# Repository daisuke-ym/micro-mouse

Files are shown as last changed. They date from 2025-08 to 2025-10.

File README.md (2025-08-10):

# マイクロマウスを作る

## はじめに

マイクロマウスは自立型ロボットが自律的に（自分の力だけで）迷路を探索し、 ゴールまで到達するものです。

競技会もあります。
詳細は
[公益財団法人ニューテクノロジー振興財団](https://www.ntf.or.jp/mouse/) 
を参照してください。

## ここで作るマイクロマウス

上記競技会ではクラシッククラスとハーフサイズクラスがありますが、
ここでは1区画180㎜のクラシッククラスを作ります。

[RT ROBOT SHOP](https://www.rt-shop.jp/index.php?main_page=product_info&products_id=4229)
等でキットが販売されていますが、高価なため個人や学生が手を出すには敷居が高いです。

そこで、3Dプリンタ、我らの秋月電子通商、中国のプリント基板業者を駆使することで
1万円以内で製作できることを目指しました。

ただし、採用しているステッピングモーター（28BYJ-48）は回転速度が遅い[^1]ため、
上記競技会で完走するのは難しいです。
主に教材用と考えてもらえればと思います。

## 主要部品

| 構成部品 | 仕様等 |
|-|-|
| マイコン | [ESP32 DevKitC](https://akizukidenshi.com/catalog/g/g115673/) |
| モーター | [28BYJ-48](https://akizukidenshi.com/catalog/g/g113256/) |
| シャーシ | 専用設計プリント基板と兼用 |
| タイヤ | 3Dプリント、TAMIYA 70144ボールキャスター |
| 電源 | 1.2V Ni-MH電池 または アルカリ乾電池 x4本 |
| 赤外線LED | [OSI5FU5111C-40](https://akizukidenshi.com/catalog/g/g103261/) |
| フォトトランジスタ | [L-51ROPT1D1](https://akizukidenshi.com/catalog/g/g104211/) |

## 開発環境

- Arduino IDE
- ESP32 ツールチェイン
- [Unistep2_mod](https://github.com/daisuke-ym/Unistep2_mod)
ライブラリ（動的に回転速度を変更できるようにしたもの）

[^1]: Unistep2 ライブラリを用いてほぼ最高速度で回しても約15rpmなので、
1区画進むのに約4秒かかります。
大会では16x16区画、256区画あるので、全探索するのに15分以上かかるため、
偶然を除いて競技時間10分以内に完走することは不可能です。

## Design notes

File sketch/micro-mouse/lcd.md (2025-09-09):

# AQM1602Y に表示する内容

```
  0123456789ABCDEF
0 XX YY  AAAA BBBB
1 SSSSS  CCCC DDDD
```

|シンボル|意味
|-----| --
|XX | マウスのX座標
|YY | マウスのY座標
|AAAA | FLセンサの値
|BBBB | FRセンサの値
|CCCC | Lセンサの値
|DDDD | Rセンサの値
|SSSSS| マウスの状態を示すフラグ(ORSCA)

|フラグ|意味
|---|--
|O|往路走行中
|R|復路走行中
|S|最短経路走行中
|C|迷路全探索完了
|A|マウスを通路中央に値調整中

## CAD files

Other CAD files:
3D-Model/28BYJ-48.ipt
3D-Model/28BYJ-48_Braket.ipt
3D-Model/28BYJ-48_Braket2.ipt
3D-Model/28BYJ-48_Braket3.ipt
3D-Model/AA-Cell-1x4.ipt
3D-Model/AA-Cell-2x2.ipt
3D-Model/AA-Cell-Holder.ipt
3D-Model/AA-Cell-x2.iam
3D-Model/AA-Cell-x4.iam
3D-Model/AE-AQM1602A.ipt
3D-Model/AQM1602XA.ipt
3D-Model/AQM1602Y.ipt
3D-Model/BH321-1P24.ipt
3D-Model/BH343.ipt
3D-Model/BallCaster-H16.ipt
3D-Model/BallCaster-H25.ipt
3D-Model/BallCaster-H35.ipt
3D-Model/BaseBoard-SPG27.ipt
3D-Model/BaseBoard-stp3.ipt
3D-Model/BaseBoard1.ipt
3D-Model/BaseBoard2.ipt
3D-Model/BaseBoard2B.ipt
3D-Model/BaseBoard3.ipt
3D-Model/Battery-Holder-1x4.ipt
3D-Model/Battery-Holder-2x2.ipt
3D-Model/Battery-Holder-SPG27-1x4-A.ipt
3D-Model/Battery-Holder2-1x4.ipt
3D-Model/Battery-Holder3-1x4.ipt
3D-Model/D-Shaft_Wheel1.ipt
3D-Model/D-Shaft_Wheel2.ipt
3D-Model/D-Shaft_Wheel3.ipt
3D-Model/D-Shaft_Wheel4.ipt
3D-Model/ESP32-DevKitC.ipt
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

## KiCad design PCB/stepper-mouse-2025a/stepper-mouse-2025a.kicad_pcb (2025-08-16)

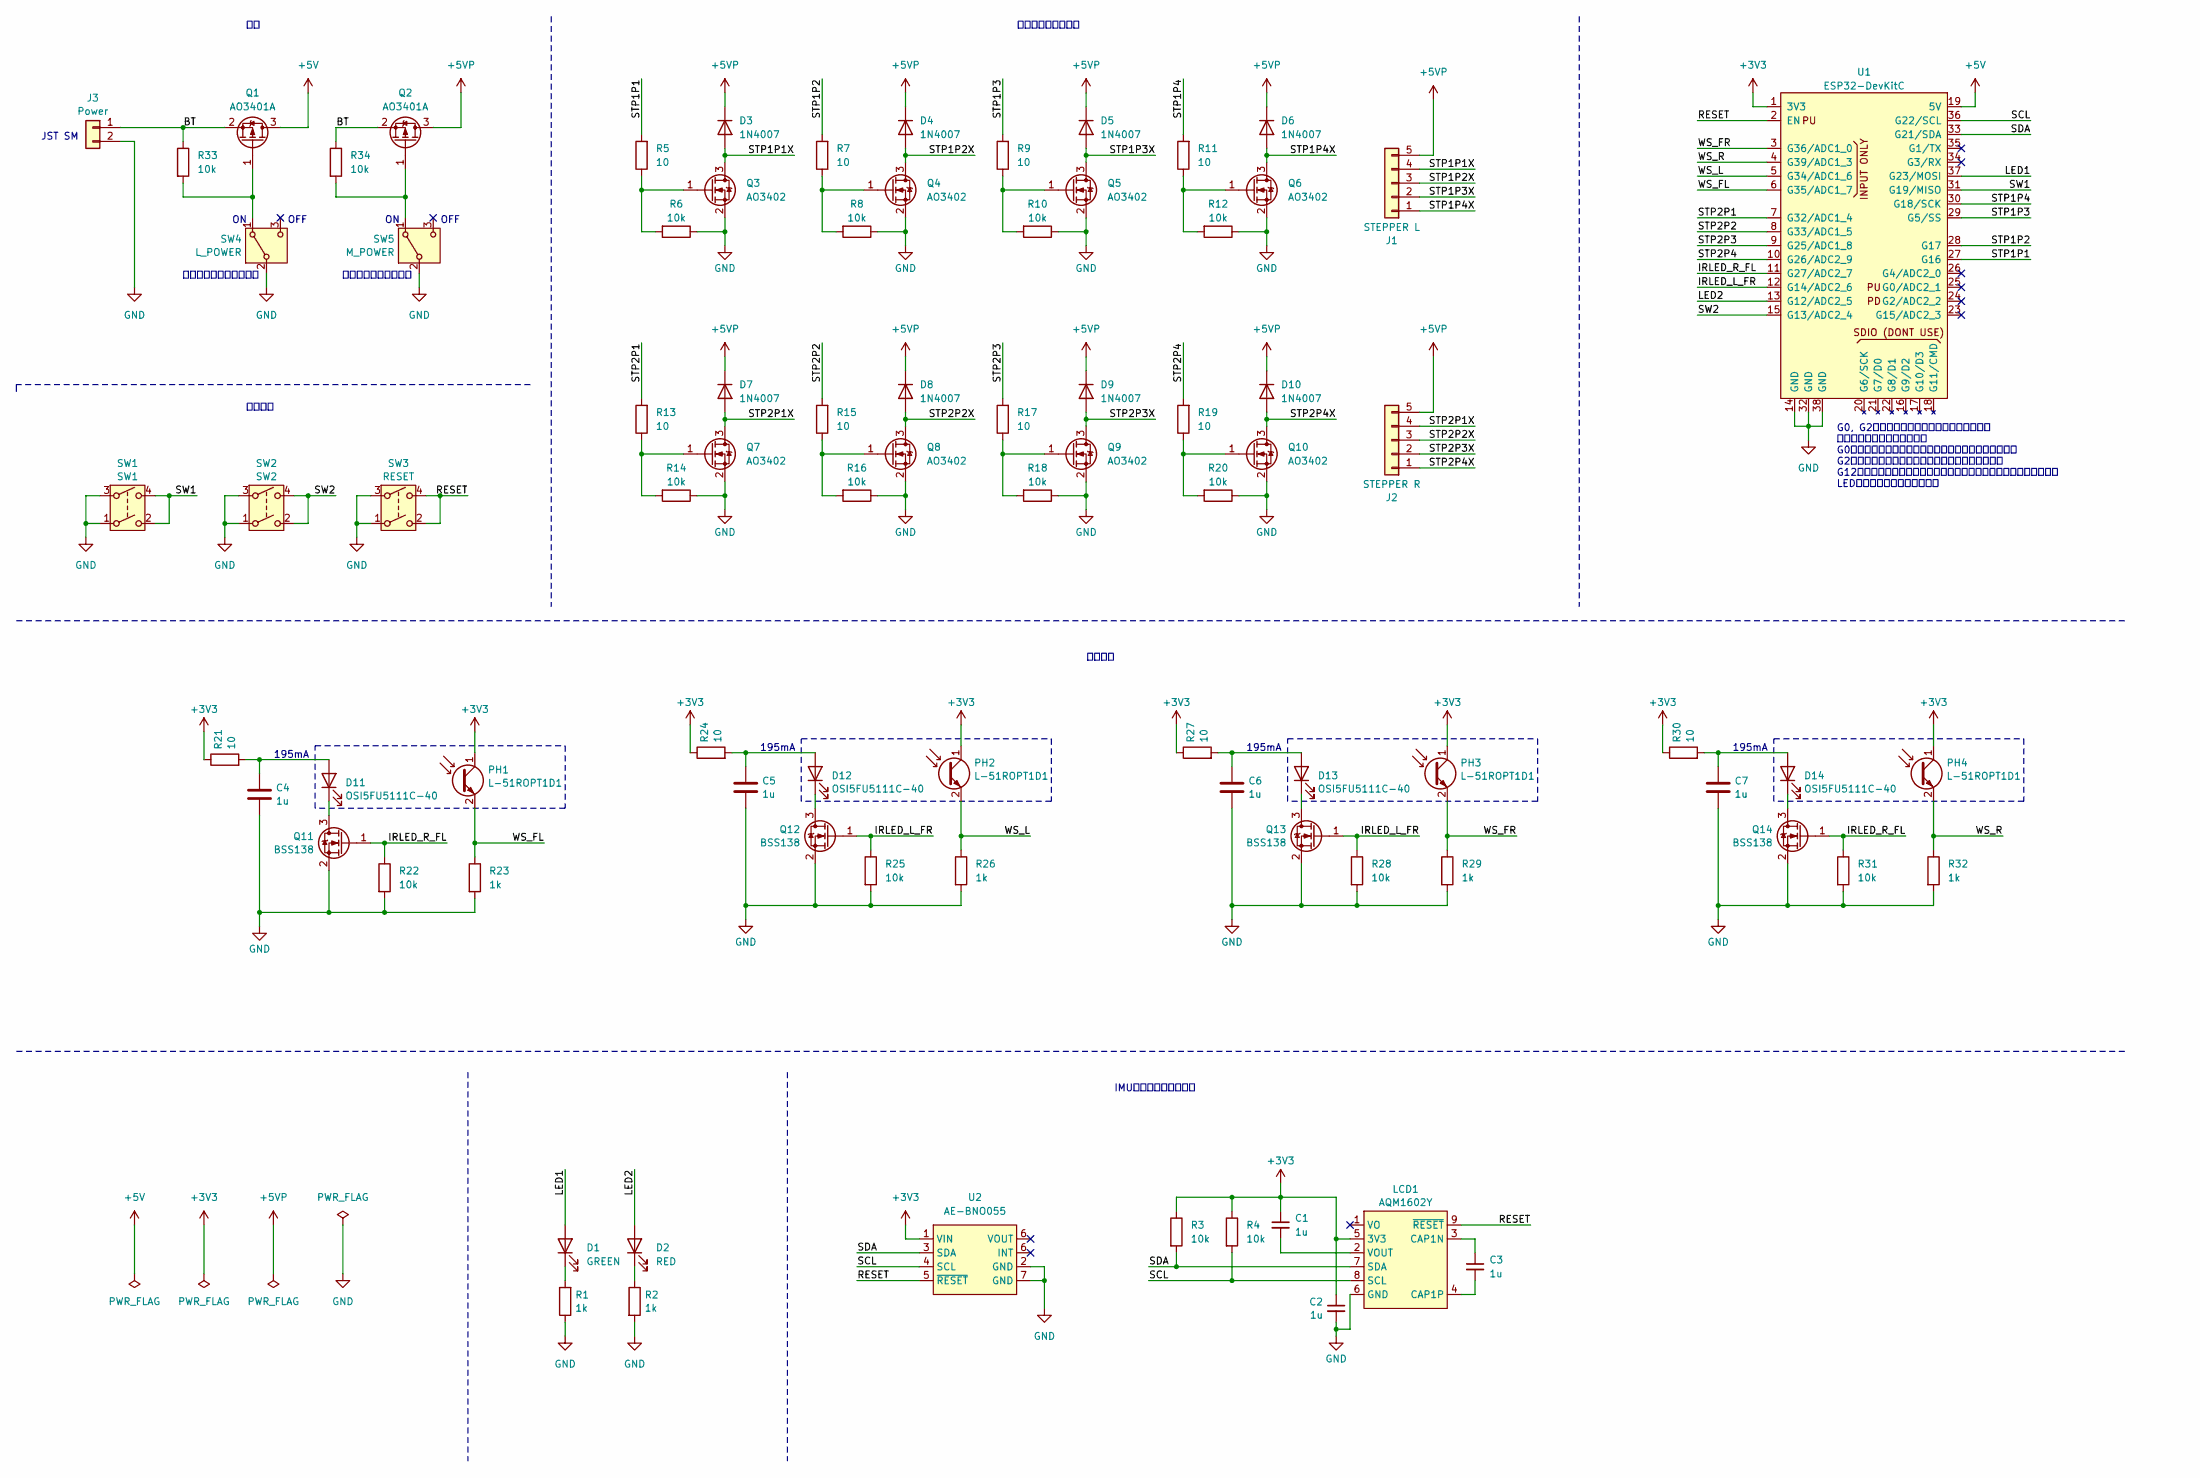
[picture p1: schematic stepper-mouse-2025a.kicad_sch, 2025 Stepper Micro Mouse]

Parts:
C1, C2, C3: 1u; C_0603_1608Metric
C4, C5, C6, C7: 1u; C_0603_1608Metric; JLCPCB C28323
D1: GREEN; LED_D5.0mm
D2: RED; LED_D5.0mm
D3, D4, D5, D6, D7, D8, D9, D10: 1N4007; D_SOD-123F
D11, D12, D13, D14: OSI5FU5111C-40; LED_D5.0mm_Horizontal_O3.81mm_Z9.0mm
J1: STEPPER L; JST_XH_B5B-XH-A_1x05_P2.50mm_Vertical
J2: STEPPER R; JST_XH_B5B-XH-A_1x05_P2.50mm_Vertical
J3: Power; PinHeader_1x02_P2.54mm_Vertical
LCD1: AQM1602Y
PH1, PH2, PH3, PH4: L-51ROPT1D1; LED_D5.0mm_Horizontal_O6.35mm_Z15.0mm
Q1, Q2: AO3401A; SOT-23
Q3, Q4, Q5, Q6, Q7, Q8, Q9, Q10: AO3402; SOT-23
Q11, Q12, Q13, Q14: BSS138; SOT-23
R1, R2, R23, R26, R29, R32: 1k; R_0603_1608Metric
R3, R4, R6, R8, R10, R12, R14, R16, R18, R20, R22, R25, R28, R31, R33, R34: 10k; R_0603_1608Metric
R5, R7, R9, R11, R13, R15, R17, R19, R21, R24, R27, R30: 10; R_0603_1608Metric
SW1: SW1; DTS-6-V-2
SW2: SW2; DTS-6-V-2
SW3: RESET; DTS-6-V-2
SW4: L_POWER; SS12D01G4
SW5: M_POWER; SS12D01G4
U1: ESP32-DevKitC
U2: AE-BNO055

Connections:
+3V3: C1.1, C2.1, LCD1.5 (3V3), PH1.1 (C), PH2.1 (C), PH3.1 (C), PH4.1 (C), R3.1, R4.1, R21.1, R24.1, R27.1, R30.1, U1.1 (3V3), U2.1 (VIN)
+5V: Q1.3 (D), U1.19 (5V)
+5VP: D3.1 (K), D4.1 (K), D5.1 (K), D6.1 (K), D7.1 (K), D8.1 (K), D9.1 (K), D10.1 (K), J1.5, J2.5, Q2.3 (D)
/BT: J3.1, Q1.2 (S), Q2.2 (S), R33.1, R34.1
/IRLED_L_FR: Q12.1 (G), Q13.1 (G), R25.1, R28.1, U1.12 (G14/ADC2_6)
/IRLED_R_FL: Q11.1 (G), Q14.1 (G), R22.1, R31.1, U1.11 (G27/ADC2_7)
/LED1: D1.2 (A), U1.37 (G23/MOSI)
/LED2: D2.2 (A), U1.13 (G12/ADC2_5)
/RESET: LCD1.9 (~RESET), SW3.2, SW3.4, U1.2 (EN), U2.5 (~RESET)
/SCL: LCD1.8 (SCL), R4.2, U1.36 (G22/SCL), U2.4 (SCL)
/SDA: LCD1.7 (SDA), R3.2, U1.33 (G21/SDA), U2.3 (SDA)
/STP1P1: R5.2, U1.27 (G16)
/STP1P1X: D3.2 (A), J1.4, Q3.3 (D)
/STP1P2: R7.2, U1.28 (G17)
/STP1P2X: D4.2 (A), J1.3, Q4.3 (D)
/STP1P3: R9.2, U1.29 (G5/SS)
/STP1P3X: D5.2 (A), J1.2, Q5.3 (D)
/STP1P4: R11.2, U1.30 (G18/SCK)
/STP1P4X: D6.2 (A), J1.1, Q6.3 (D)
/STP2P1: R13.2, U1.7 (G32/ADC1_4)
/STP2P1X: D7.2 (A), J2.4, Q7.3 (D)
/STP2P2: R15.2, U1.8 (G33/ADC1_5)
/STP2P2X: D8.2 (A), J2.3, Q8.3 (D)
/STP2P3: R17.2, U1.9 (G25/ADC1_8)
/STP2P3X: D9.2 (A), J2.2, Q9.3 (D)
/STP2P4: R19.2, U1.10 (G26/ADC2_9)
/STP2P4X: D10.2 (A), J2.1, Q10.3 (D)
/SW1: SW1.2, SW1.4, U1.31 (G19/MISO)
/SW2: SW2.2, SW2.4, U1.15 (G13/ADC2_4)
/WS_FL: PH1.2 (E), R23.1, U1.6 (G35/ADC1_7)
/WS_FR: PH3.2 (E), R29.1, U1.3 (G36/ADC1_0)
/WS_L: PH2.2 (E), R26.1, U1.5 (G34/ADC1_6)
/WS_R: PH4.2 (E), R32.1, U1.4 (G39/ADC1_3)
GND: C2.2, C4.2, C5.2, C6.2, C7.2, J3.2, LCD1.6 (GND), Q3.2 (S), Q4.2 (S), Q5.2 (S), Q6.2 (S), Q7.2 (S), Q8.2 (S), Q9.2 (S), Q10.2 (S), Q11.2 (S), Q12.2 (S), Q13.2 (S), Q14.2 (S), R1.1, R2.2, R6.1, R8.1, R10.1, R12.1, R14.1, R16.1, R18.1, R20.1, R22.2, R23.2, R25.2, R26.2, R28.2, R29.2, R31.2, R32.2, SW1.1, SW1.3, SW2.1, SW2.3, SW3.1, SW3.3, SW4.2 (B), SW5.2 (B), U1.14 (GND), U1.32 (GND), U1.38 (GND), U2.2 (GND), U2.7 (GND)
unnamed: D1.1 (K), R1.2
unnamed: D2.1 (K), R2.1
unnamed: C4.1, D11.2 (A), R21.2
unnamed: D11.1 (K), Q11.3 (D)
unnamed: C5.1, D12.2 (A), R24.2
unnamed: D12.1 (K), Q12.3 (D)
unnamed: C6.1, D13.2 (A), R27.2
unnamed: D13.1 (K), Q13.3 (D)
unnamed: C7.1, D14.2 (A), R30.2
unnamed: D14.1 (K), Q14.3 (D)
unnamed: C3.1, LCD1.3 (CAP1N)
unnamed: C3.2, LCD1.4 (CAP1P)
unnamed: C1.2, LCD1.2 (VOUT)
unnamed: Q1.1 (G), R33.2, SW4.1 (A)
unnamed: Q2.1 (G), R34.2, SW5.1 (A)
unnamed: Q3.1 (G), R5.1, R6.2
unnamed: Q4.1 (G), R7.1, R8.2
unnamed: Q5.1 (G), R9.1, R10.2
unnamed: Q6.1 (G), R11.1, R12.2
unnamed: Q7.1 (G), R13.1, R14.2
unnamed: Q8.1 (G), R15.1, R16.2
unnamed: Q9.1 (G), R17.1, R18.2
unnamed: Q10.1 (G), R19.1, R20.2

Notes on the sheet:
モータ用電源スイッチ
195mA
スイッチ
OFF
JST SM
G0, G2はブートストラップに使用するので、 接続する機器に注意が必要。 G0はプルアップされているので、スイッチは問題ない。 G2はプルダウンされているので、特に注意が必要。 G12はフラッシュ書き込み時の電圧設定にかかわるので注意が必要。 LEDをつなぐ分には問題ない。
IMU，液晶ディスプレイ
ロジック用電源スイッチ
ステッピングモータ
壁センサ

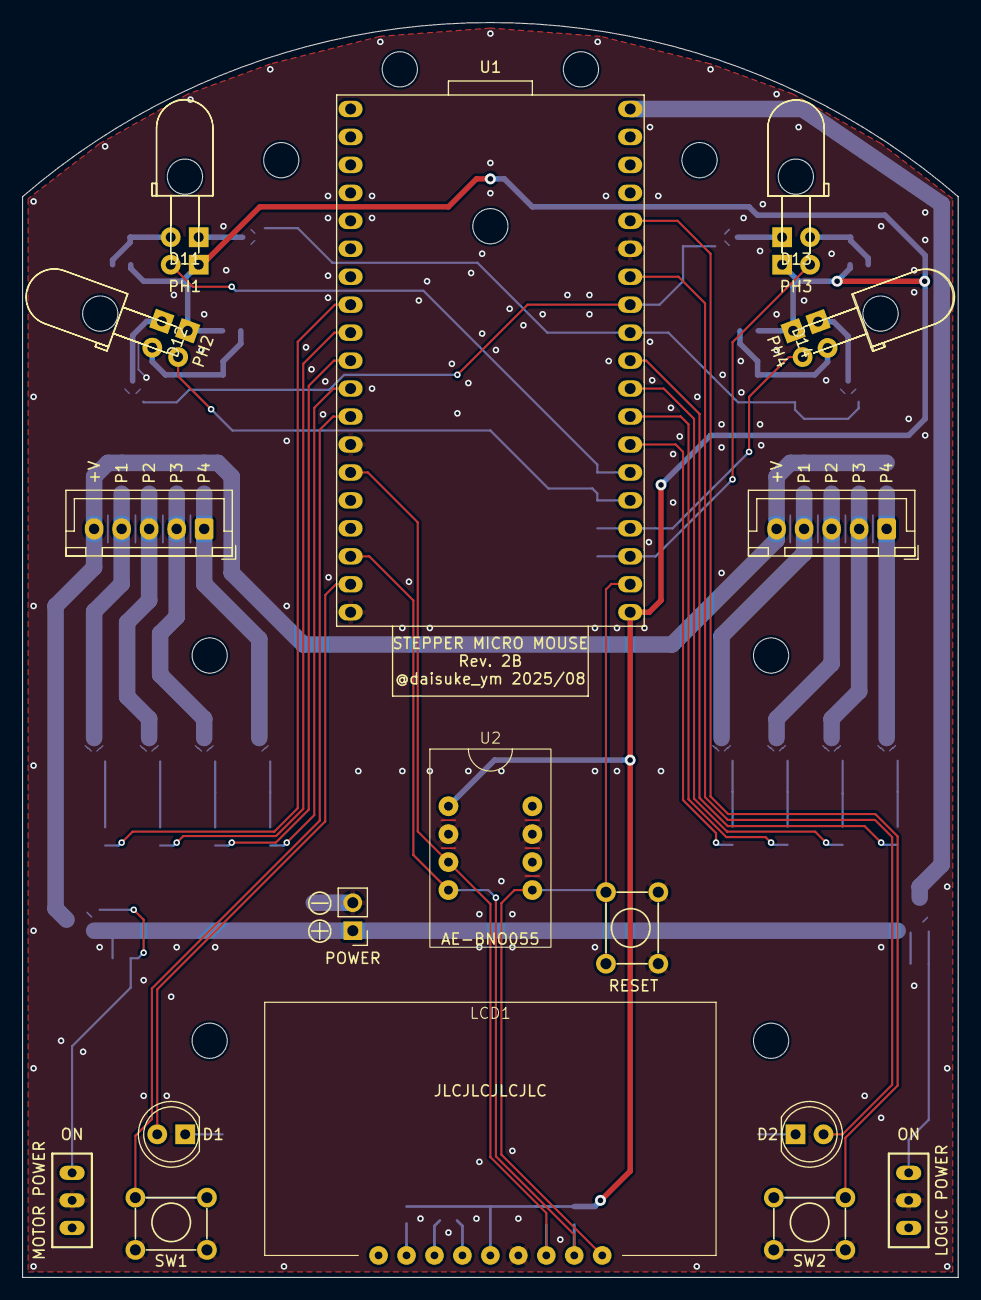
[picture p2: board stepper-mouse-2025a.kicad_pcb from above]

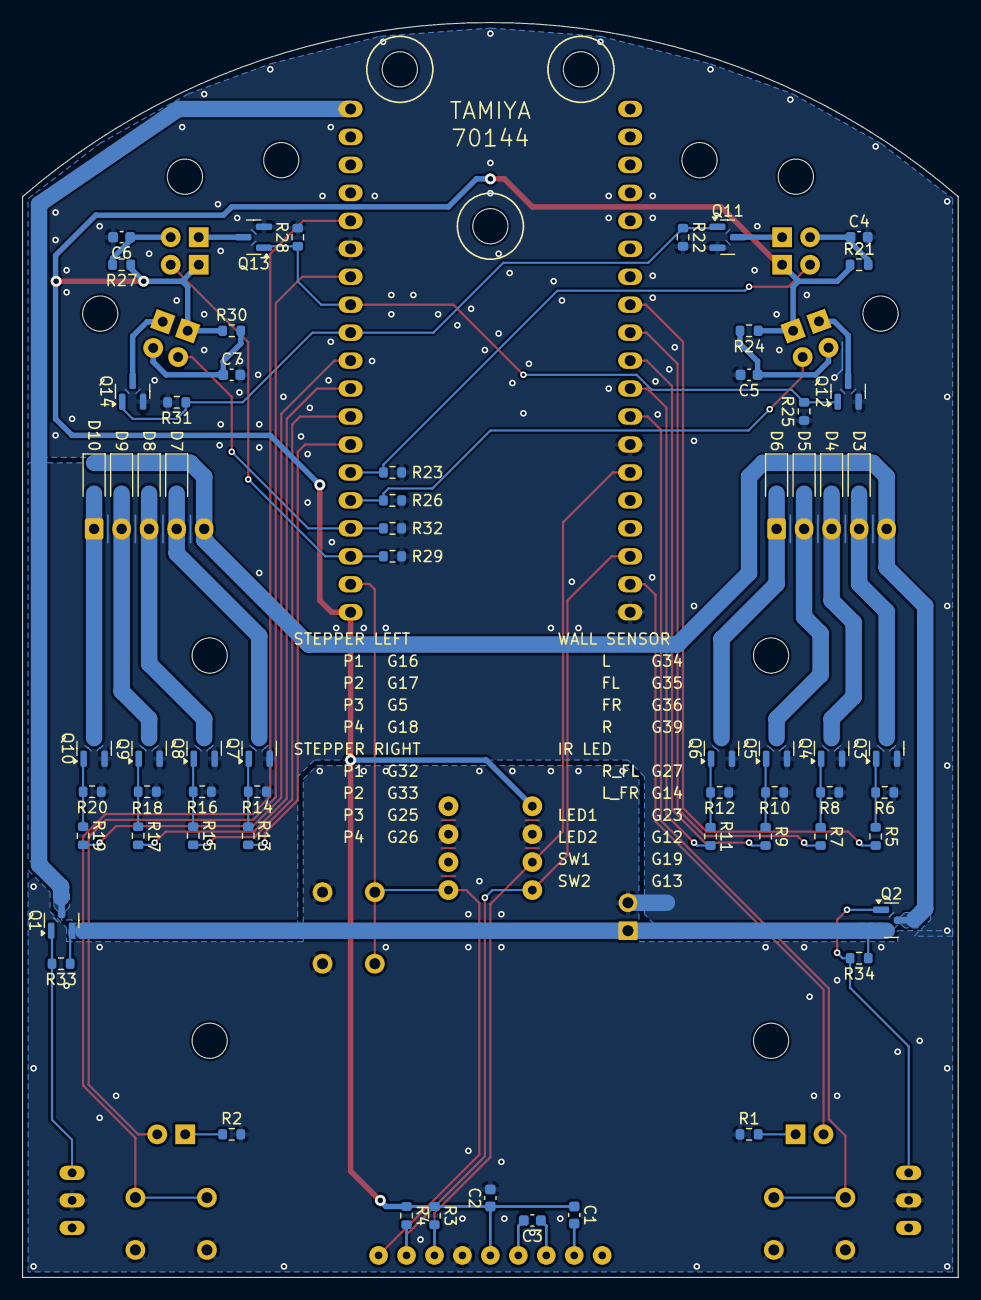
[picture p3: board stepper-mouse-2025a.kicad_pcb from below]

Board: 2 copper layers, 85.0 x 114.0 mm, 85 parts (68 on the bottom side), 57 nets.

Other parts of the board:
TAMIYA70144: VAL**; TAMIYA70144

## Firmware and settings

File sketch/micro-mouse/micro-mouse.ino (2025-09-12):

#include <BluetoothSerial.h>
#include <Unistep2_mod.h>
#include <ST7032_asukiaaa.h>
#include <math.h>
#include <Wire.h>
#include <Adafruit_BNO055.h>
#include "parameters.h"
#include "defines.h"

// ----------------------------------------------------------------------
void setup() {
  // serial
  Serial.begin(115200);
  SerialBT.begin(BT_NAME); // Bluetooth シリアルの初期化
  // センサの初期設定
  analogReadResolution(12);
  pinMode(SENSOR_FL, INPUT);
  pinMode(IRLED_L_FR, OUTPUT);
  pinMode(IRLED_R_FL, OUTPUT);
  // LCDの初期化
  lcd.begin(16, 2);
  lcd.setContrast(40);
  lcd.clear();
  // スイッチとLEDの初期設定
  pinMode(SW1, INPUT_PULLUP);
  pinMode(SW2, INPUT_PULLUP);
  pinMode(LED1, OUTPUT);
  pinMode(LED2, OUTPUT);
  // BNO055 の初期化
  if (!bno.begin()) {
    Serial.print("BNO055 not detected. Check wiring.");
    while (1);
  }
  bno.setExtCrystalUse(false);
  // BNO055 の初期化完了まで待つ
  delay(1000);

  // センサの値を読むタスク
  //xTaskCreateUniversal(read_sensor, "task_read_sensor", 8192, NULL, 1, NULL, APP_CPU_NUM);
  xTaskCreateUniversal(read_sensor_sma, "task_read_sensor_sma", 8192, NULL, 1, NULL, APP_CPU_NUM);
  // センサの値を出力するタスク
  xTaskCreateUniversal(print_sensor, "task_print_sensor", 8192, NULL, 1, NULL, APP_CPU_NUM);
  // LCDに現在位置を出力するタスク
  xTaskCreateUniversal(print_pos, "task_print_pos", 8192, NULL, 1, NULL, APP_CPU_NUM);
  // LCDにフラグを出力するタスク
  xTaskCreateUniversal(print_state_flags, "task_print_state_flags", 8192, NULL, 1, NULL, APP_CPU_NUM);
  // ステッパの値を出力するタスク
  //xTaskCreatePinnedToCore(print_steps, "task_print_steps", 8192, NULL, 1, NULL, APP_CPU_NUM);
  // BNO055 の値を読むタスク
  xTaskCreatePinnedToCore(read_bno, "task_read_bno", 8192, NULL, 1, NULL, APP_CPU_NUM);
  // Bluetooth に値を出力するタスク
  //xTaskCreatePinnedToCore(print_serialbt, "task_print_serialbt", 8192, NULL, 1, NULL, APP_CPU_NUM);

  // 迷路の初期化
  init_maze();
}

// ----------------------------------------------------------------------
void loop() {
  static unsigned long start_time = millis();

  if (millis() - start_time > 2000) {
    SERIAL_OUT.println(millis());
    start_time = millis();
  }
  test_decide_direction_tremaux();
  test_run_shortest_path();
}

// ----------------------------------------------------------------------
void read_sensor(void *pvParameters) {
  int ir_on[2], ir_off[2];

  while (1) {
    // 全部の IRLED を OFF にしてセンサの値を読む
    digitalWrite(IRLED_L_FR, LOW);
    digitalWrite(IRLED_R_FL, LOW);
    ir_off[0] = analogRead(SENSOR_R);
    ir_off[1] = analogRead(SENSOR_FL);
    // R と FL の IRLED を ON にしてセンサの値を読む
    digitalWrite(IRLED_R_FL, HIGH);
    ir_on[0] = analogRead(SENSOR_R);
    ir_on[1] = analogRead(SENSOR_FL);
    SS_R = ir_on[0] - ir_off[0];
    SS_FL = ir_on[1] - ir_off[1];
    // 全部の IRLED を OFF にしてセンサの値を読む
    digitalWrite(IRLED_L_FR, LOW);
    digitalWrite(IRLED_R_FL, LOW);
    ir_off[0] = analogRead(SENSOR_L);
    ir_off[1] = analogRead(SENSOR_FR);
    // L と FR の IRLED を ON にしてセンサの値を読む
    digitalWrite(IRLED_L_FR, HIGH);
    ir_on[0] = analogRead(SENSOR_L);
    ir_on[1] = analogRead(SENSOR_FR);
    SS_L = ir_on[0] - ir_off[0];
    SS_FR = ir_on[1] - ir_off[1];
    // 全部の IRLED を OFF にする
    digitalWrite(IRLED_L_FR, LOW);
    digitalWrite(IRLED_R_FL, LOW);
    // Task を回すうえで必ず必要な delay
    delay(1);
  }
}

// ----------------------------------------------------------------------
// センサの値を読み取るタスク(単純移動平均版)
void read_sensor_sma(void *pvParameters) {
  int ir_on[2], ir_off[2];
  int ss_l[10], ss_r[10], ss_fl[10], ss_fr[10];
  int index = 0;

  while (1) {
    if (index >= 10) {
      index = 0;
    }
    // 全部の IRLED を OFF にしてセンサの値を読む
    digitalWrite(IRLED_L_FR, LOW);
    digitalWrite(IRLED_R_FL, LOW);
    ir_off[0] = analogRead(SENSOR_R);
    ir_off[1] = analogRead(SENSOR_FL);
    // R と FL の IRLED を ON にしてセンサの値を読む
    digitalWrite(IRLED_R_FL, HIGH);
    ir_on[0] = analogRead(SENSOR_R);
    ir_on[1] = analogRead(SENSOR_FL);
    ss_r[index] = ir_on[0] - ir_off[0];
    ss_fl[index] = ir_on[1] - ir_off[1];
    // 全部の IRLED を OFF にしてセンサの値を読む
    digitalWrite(IRLED_L_FR, LOW);
    digitalWrite(IRLED_R_FL, LOW);
    ir_off[0] = analogRead(SENSOR_L);
    ir_off[1] = analogRead(SENSOR_FR);
    // L と FR の IRLED を ON にしてセンサの値を読む
    digitalWrite(IRLED_L_FR, HIGH);
    ir_on[0] = analogRead(SENSOR_L);
    ir_on[1] = analogRead(SENSOR_FR);
    ss_l[index] = ir_on[0] - ir_off[0];
    ss_fr[index] = ir_on[1] - ir_off[1];
    // 全部の IRLED を OFF にする
    digitalWrite(IRLED_L_FR, LOW);
    digitalWrite(IRLED_R_FL, LOW);
    // 単純移動平均を求める
    SS_L = 0;
    SS_R = 0;
    SS_FL = 0;
    SS_FR = 0;
    for (int i = 0; i < 10; i++) {
      SS_L += ss_l[i];
      SS_R += ss_r[i];
      SS_FL += ss_fl[i];
      SS_FR += ss_fr[i];
    }
    SS_L = SS_L / 10;
    SS_R = SS_R / 10;
    SS_FL = SS_FL / 10;
    SS_FR = SS_FR / 10;
    index++;
    // Task を回すうえで必ず必要な delay
    delay(1);
  }
}

// ----------------------------------------------------------------------
void print_sensor(void *pvParameters) {
  while (1) {
    lcd.setCursor(7, 0);
    lcd.printf("%4d %4d", SS_FL, SS_FR);
    lcd.setCursor(7, 1);
    lcd.printf("%4d %4d", SS_L, SS_R);
    /*
    Serial.print(SS_L);
    Serial.print("\t");
    Serial.print(SS_FL);
    Serial.print("\t");
    Serial.print(SS_FR);
    Serial.print("\t");
    Serial.print(SS_R);
    Serial.println();
    */
    delay(250);
  }
}

// ----------------------------------------------------------------------
void print_steps(void *args) {
  static unsigned long lcd_period = 0;

  while (1) {
    lcd.setCursor(0, 0);
    lcd.print(stepperL.stepsToGo());
    lcd.print("   ");
    lcd.setCursor(8, 0);
    lcd.print(stepperR.stepsToGo());
    lcd.print("   ");
    lcd_period = millis();
    delay(100);
  }
}

// ----------------------------------------------------------------------
void read_bno(void *pvParameters) {

  while (1) {
    imu::Vector<3> IMU_EULER = bno.getVector(Adafruit_BNO055::VECTOR_EULER);
    DIR_X = IMU_EULER.x();
    DIR_Y = IMU_EULER.y();
    DIR_Z = IMU_EULER.z();
    /*
    // デバッグ用にシリアル出力
    Serial.print("X: ");
    Serial.print(DIR_X);
    Serial.print(" Y: ");
    Serial.print(DIR_Y);
    Serial.print(" Z: ");
    Serial.println(DIR_Z);
    */
    // Task を回すうえで必ず必要な delay
    delay(10);
  }
}

// ----------------------------------------------------------------------
void print_serialbt(void *pvParameters) {
  while (1) {
    SerialBT.println(millis());
    // Task を回すうえで必ず必要な delay
    delay(1000);
  }
}

// ----------------------------------------------------------------------
// LCDに現在座標を表示するタスク
void print_pos(void *pvParameters) {
  while (1) {
    lcd.setCursor(0, 0);
    lcd.printf("%2d %2d", MAZE.x, MAZE.y);
    delay(500);
  }
}

// ----------------------------------------------------------------------
// LCDにフラグを表示するタスク
void print_state_flags(void *pvParameters) {
  while (1) {
    lcd.setCursor(0, 1);
    lcd.printf("%c%c%c%c%c", 
      (STATE_FLAG & SF_RUNNING_O) ? 'O' : '-', 
      (STATE_FLAG & SF_RUNNING_R) ? 'R' : '-',
      (STATE_FLAG & SF_RUNNING_S) ? 'S' : '-', 
      (STATE_FLAG & SF_SEARCH_COMPLETE) ? 'C' : '-', 
      (STATE_FLAG & SF_ADJUST_TO_CENTER) ? 'A' : '-');
    delay(500);
  }
}

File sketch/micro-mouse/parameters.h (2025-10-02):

/*
  機体固有の値を定義するヘッダファイル
  ここを変更することで、機体に合わせた調整が可能
*/

// ----------------------------------------------------------------------
// ピンの定義
// センサと赤外線LED
const int SENSOR_FL = 35;
const int SENSOR_L  = 34;
const int SENSOR_R  = 39;
const int SENSOR_FR = 36;
const int IRLED_R_FL = 27;
const int IRLED_L_FR = 14;
// スイッチとLED
const int SW1 = 19;
const int SW2 = 13;
const int LED1 = 23;
const int LED2 = 12;
// ステッピングモータ左
const int STP1P1 = 16;
const int STP1P2 = 17;
const int STP1P3 = 5;
const int STP1P4 = 18;
// ステッピングモータ右
const int STP2P1 = 32;
const int STP2P2 = 33;
const int STP2P3 = 25;
const int STP2P4 = 26;

// ----------------------------------------------------------------------
// Bluetooth のデバイス名
const char BT_NAME[] = "ESP32_MicroMouse";

// ----------------------------------------------------------------------
// ステッピングモータ
const double STEPS = 4096.0; // 1回転するのに必要なステップ数
const unsigned long DEFAULT_STEP_DELAY = 1000; // 回転速度（unistep2_mod でのディレイ値：小さいほど回転が速い）

// ----------------------------------------------------------------------
// 車体の数値
const double WHEEL_D = 63.0; // ホイールの直径(mm)
const double TREAD = 97.0;  // トレッド
const double MMPS = M_PI * WHEEL_D / STEPS; // 1ステップで進む距離(milli meter per step)

// ----------------------------------------------------------------------
// 壁があるかどうかの閾値
const int WALL_TV = 1000; // 壁があるとみなすセンサ値の閾値
const int FL_LIMIT = 3860; // センサ値の上限(これ以上行くと壁に衝突する)
const int FR_LIMIT = 3955; // センサ値の上限(これ以上行くと壁に衝突する)

// ----------------------------------------------------------------------
// 壁センサ(SS_L)の値と壁までの距離マップ
const int WALL_DIST[] = {
  3818, // 0mm
  3795, // 5mm
  3725, // 10mm
  3525, // 15mm
  2950, // 20mm
  2520, // 25mm
  2170, // 30mm
  1870, // 35mm
  1660, // 40mm
  1465, // 45mm
  1285, // 50mm
  1175, // 55mm
  1065, // 60mm
};
// 通路中央に置いたときの壁までの距離
const int WALL_DIST_CENTER = 33;
// 通路中央に置いたときの SS_L の値
const int SS_L_CENTER = 2000;

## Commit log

2025-07-24 Inventorのプロジェクトファイルを追加
2025-07-24 3Dモデルを追加
    [28BYJ-48.ipt, 28BYJ-48_Braket.ipt, AA-Cell-1x4.ipt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]
2025-07-24 .gitignoreを追加
2025-07-24 28BYJ-48を使用したタイプの基板データを追加
    [stepper-mouse-2025a.kicad_pcb, stepper-mouse-2025a.kicad_sch]
2025-07-25 バッテリーホルダーを追加 ブラケットの形状を修正 アセンブリを更新
    [28BYJ-48_Braket2.ipt, BaseBoard-stp3.ipt, Battery-Holder-1x4.ipt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]
2025-07-27 Rev.1から使い勝手の悪いところを修正したもの
    [stepper-mouse-2025a.kicad_pcb, stepper-mouse-2025a.kicad_sch]
2025-07-28 バッテリーホルダーの形状を修正したものを追加
    [Battery-Holder2-1x4.ipt]
2025-07-29 電池ボックス BH-343-3B も乗るように修正した
    [Battery-Holder2-1x4.ipt]
2025-07-31 タイヤ代わりのスポンジを貼るために直径を小さくしたものを追加
    [Wheel-D45A.ipt]
2025-07-31 アセンブリを更新
    [Stepper-28BYJ_asm.iam, test-model-2025stp3.iam]
2025-07-31 .gitignore を更新し、JLCPCB プラグインのフォルダを無視するようにした。
2025-07-31 コードを書き始めた。 まずは指定距離(mm)移動と指定角度(度)回転のテストを追加。
2025-07-31 タイヤを中心にして旋回する関数を追加した。
2025-08-01 BNO055 IMU センサの値を読むタスクを追加した。
2025-08-04 IMUからオイラー角を取得し、指定角度の回転を実行する機能を追加
2025-08-04 ソースコードを分割した
2025-08-04 不要な変数を削除した
2025-08-04 インデントを修正した
2025-08-05 Rev.2 基板用にピン割り当てを変更
2025-08-05 グローバル変数を別ファイルに移した
2025-08-05 不要なグローバル変数を削除した
2025-08-06 左手法で迷路を探索するコードを追加した。
2025-08-07 LED操作関数を別ファイルにした。
2025-08-07 print_maze() 関数で、通過済みのセルだけを表示するように変更した。
2025-08-08 print_maze() 関数の出力を BluetoothSerial に変更した。
2025-08-08 update_pos_and_walls() において、セルの通過回数を記録するようにした。 print_maze() において、セルの通過回数を出力するようにした。
2025-08-08 _MAZE 構造体からゴール位置を削除し、代わりに定数 MAZE_GOAL_X と MAZE_GOAL_Y を使用するように変更した。 ゴールに到達した後、スタート地点に戻るようにした。
2025-08-08 最短経路を求めるための等高線図を作成する関数を実装した。
2025-08-08 print_maze() 関数において、ループを回す条件を修正した。
2025-08-08 ファイル名を変更した。
2025-08-08 デバッグ・テスト用の部分を削除した。
2025-08-08 シリアルの出力先を有線とBluetoothの切り替えが簡単にできるようにした。
2025-08-10 等高線図から最短経路を探索する関数を追加した。
2025-08-10 README.md に概要を追加した。
2025-08-10 全角スペースを削除した。
2025-08-13 車体が通路の中央からずれたとき補正する動作を入れた。
2025-08-13 壁センサの読み込みを単純移動平均に変更した。
2025-08-16 Rev.2のエラッタを修正
    [stepper-mouse-2025a.kicad_pcb, stepper-mouse-2025a.kicad_sch]
2025-08-17 ファイル名を変更した
    [test-model-28BYJ.iam]
2025-08-17 別のステッピングモータ（SPG27）を使ったマイクロマウスの3Dモデルを追加した。 まだ構想段階。
    [BaseBoard-SPG27.ipt, SPG27.ipt, SPG27_Braket.ipt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]
2025-08-19 用語の修正に伴うコミット（変数、関数名の変更など）
2025-08-19 最短経路で走行する関数を追加した。
2025-08-20 search-functions.ino から run-functions.ino にいくつかの関数を移動した。
2025-08-28 トレモー法による迷路探索アルゴリズムの実装が完了した。 ただし、帰り道の探索がうまく動かないので、通過済み配列を初期化することで対応している。
2025-08-29 進行方向を更新するコードが冗長だったので、関数を作ってまとめた。
2025-08-29 ゴールからスタートに戻るとき、通過回数マップをリセットしなければ戻れなかったのを リセットせずに戻れるように修正した。
2025-08-29 左手法の関数を別ファイルに移動した。 search-lefthand.ino
    search-functions.ino -> search-common-functions.ino
    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
2025-08-29 左と前に進める状況において、左と前の通過回数が同じ場合に左を優先するように変更した。
2025-08-29 最短経路を求める際、スタート位置とゴール位置を引数で指定できるように変更した。
2025-09-01 make_steps_map() 関数の引数を変更し、スタート位置を指定できるようにした。 update_steps_map() 関数の引数を変更し、スタート位置（マップ更新の終了地点）を指定できるようにした。
2025-09-02 run_shortest_path() 関数に引数を追加して、開始座標、目標座標、開始方向を指定できるようにした。 resolve_shortest_path() 関数のバグを修正した。
    [resolve-functions.ino, test-functions.ino]
2025-09-02 復路の途中で全区間の探索が完了したら、その時点で最短経路でスタート地点に戻るようにした。
2025-09-02 SPG27 を使ったマイクロマウスの基板データを追加した。
    [stepper-mouse-2025b.kicad_pcb, stepper-mouse-2025b.kicad_sch]
2025-09-02 冗長なif文を簡略化した。
2025-09-02 デバッグ用のシリアル出力をコメントアウトした。
2025-09-02 LCDに現在座標を表示させていた部分を別の関数に移動した。
2025-09-02 最短経路で走行中も現在位置を表示するようにした。
2025-09-02 最短経路を求める処理で、壁情報を考慮していなかったのを修正。
2025-09-02 SPG27基板に合わせて3Dモデルを修正した。
    [BaseBoard-SPG27.ipt, LiPo-7.4V-69x35x18.ipt, SPG27_Braket.ipt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]
2025-09-05 update_steps_map() 関数に type 引数を追加し、 歩数図作成に通常モードか直進優先モードを選べるようにした。
2025-09-05 ホイールの形状を変更したので、defines.hの数値を変更した。
    [Wheel-D45B.ipt]
2025-09-05 直前のコミットでの調整が甘かったので、再度調整した。
2025-09-05 直進時、前のセンサを監視することで壁に衝突するのを防ぐようにした。
2025-09-08 ホイールを大きくした 28BYJ-48 を使ったモデルデータを追加した。
    [28BYJ-48_Braket3.ipt, Battery-Holder3-1x4.ipt, O-ring_D63.ipt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]
2025-09-09 迷路の表示を見やすくした。
2025-09-09 現在位置をLCDに表示する処理を update_pos_and_walls() から分離し、 専用のタスク print_pos() として実装した。
2025-09-09 マウスの状態を示すフラグLCDに表示するようにした。
2025-09-09 typo を修正した。
2025-09-10 SPG27 用のモデルをいろいろ修正した。
    [BaseBoard-SPG27.ipt, Battery-Holder-SPG27-1x4-A.ipt, LED-Spacer2.ipt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]
2025-09-10 defines.h に車体固有の値とその他の定義が混ざっていたので、 車体固有の値を parameters.h に分離した。
2025-09-12 parameters.h にグローバル変数が混ざっていたので defines.h に移動した。 車体を中央に戻す処理で使う定数 WALL_DIST_CENTER を parameters.h に追加した。 また、Bluetooth のデバイス名を BT_NAME として parameters.h に追加した。 micro-mouse.ino の setup() 内で Bluetooth シリアル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
2025-09-12 print_maze() で通過回数を表示する処理を消してしまっていたので戻した。
2025-09-12 26e09ce1ccfe875c65f47be97e9317f61779f93f のコミットで、 センサの値(現在値) の定義を削除してしまったため、書き戻した。
2025-09-16 SPG27版でホイール径を30mmにしたやつのモデルデータを追加した。 一部パーツの修正あり。
    [Battery-Holder-SPG27-1x4-A.ipt, O-ring_D31.ipt, SensorBoard-SPG27.ipt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]
2025-09-26 同じファイル名で内容が異なるものをマージから除外する設定ファイル。
2025-10-01 .gitattributes ファイルを更新
2025-10-01 ホイール径を63㎜にしたモデルデータを追加
    [Battery-Holder3-1x4.ipt, Wheel-D63C.ipt, test-model-28BYJ_2.iam]
2025-10-02 ホイール径を63㎜に変更したので、パラメータを調整した。
2025-10-03 分岐点で方向転換をピボットターン（片側の車輪を中心に回転）にするテスト
2025-10-07 IMUが認識されない場合に備えて、IMUが認識された場合にのみIMUの値を読むタスクを生成するように変更した。 不要なコメントアウトを削除した。
2025-11-01 説明用パネルデータを追加
2026-05-13 2026年度版の基板データを追加
